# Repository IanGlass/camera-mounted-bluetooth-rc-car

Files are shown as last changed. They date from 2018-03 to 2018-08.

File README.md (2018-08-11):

# Camera Mounted Bluetooth Model Car

Embedded systems six-person project (known as "Wacky Racers") to design and implement a camera mounted, Bluetooth controlled, model car. The project had a requirement that three separate 4-layer boards (1:motor driver, 2:camera driver and 3:main/wifi communications) were developed each with their own microcontroller and communicated over a common I2C bus. STM32F4 microcontrollers were selected for the project.

## Camera Board

<p align="center">
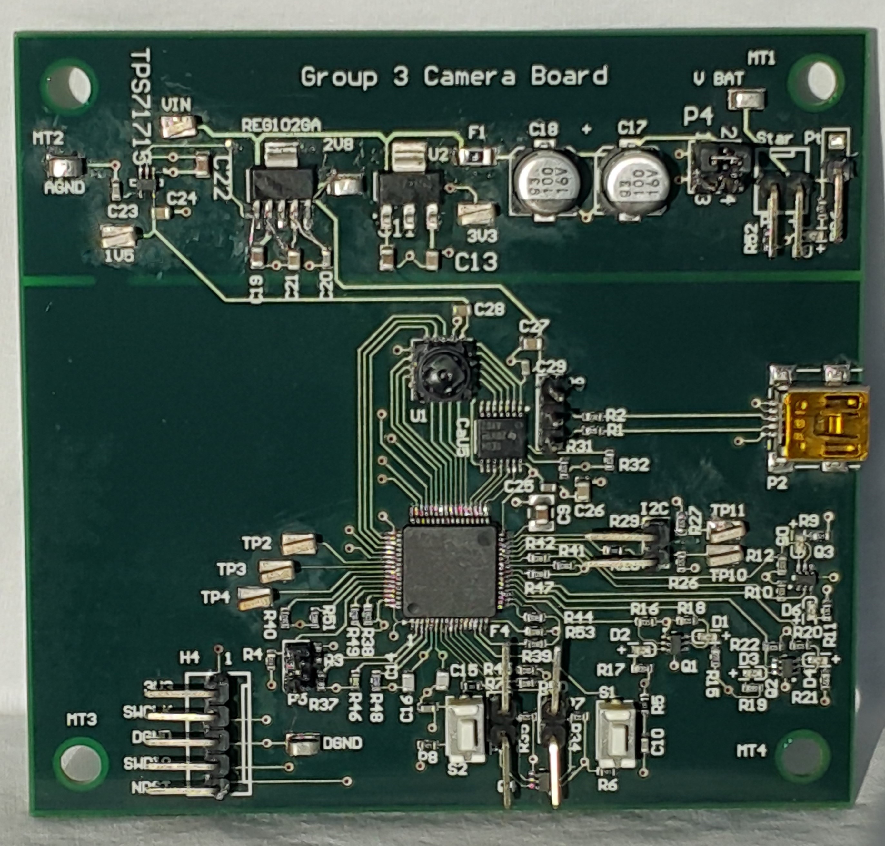
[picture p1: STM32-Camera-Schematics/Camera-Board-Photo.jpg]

</p>
<p align="center">
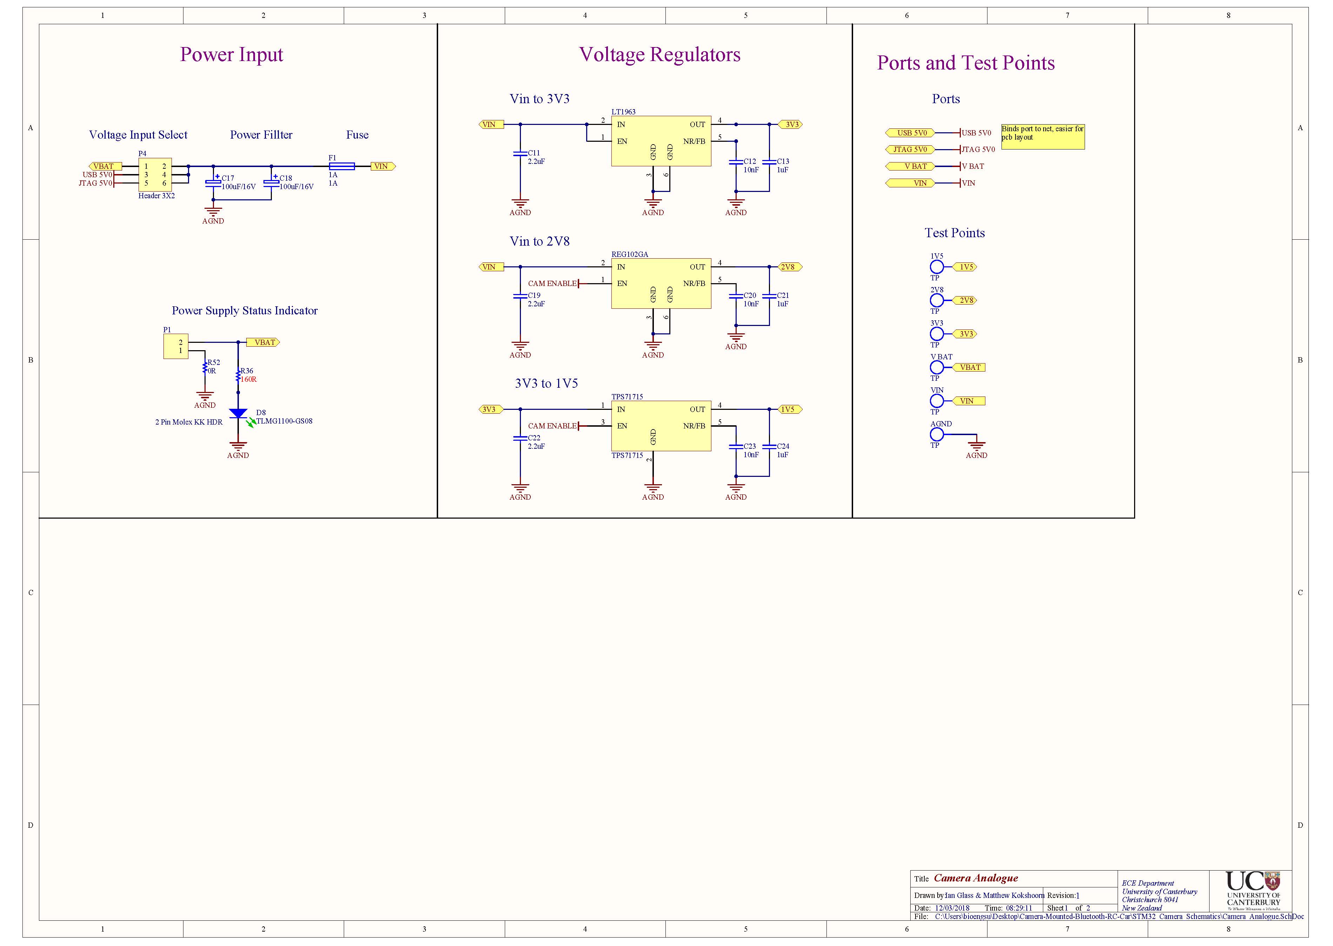
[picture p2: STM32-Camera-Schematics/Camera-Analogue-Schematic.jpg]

</p>
<p align="center">
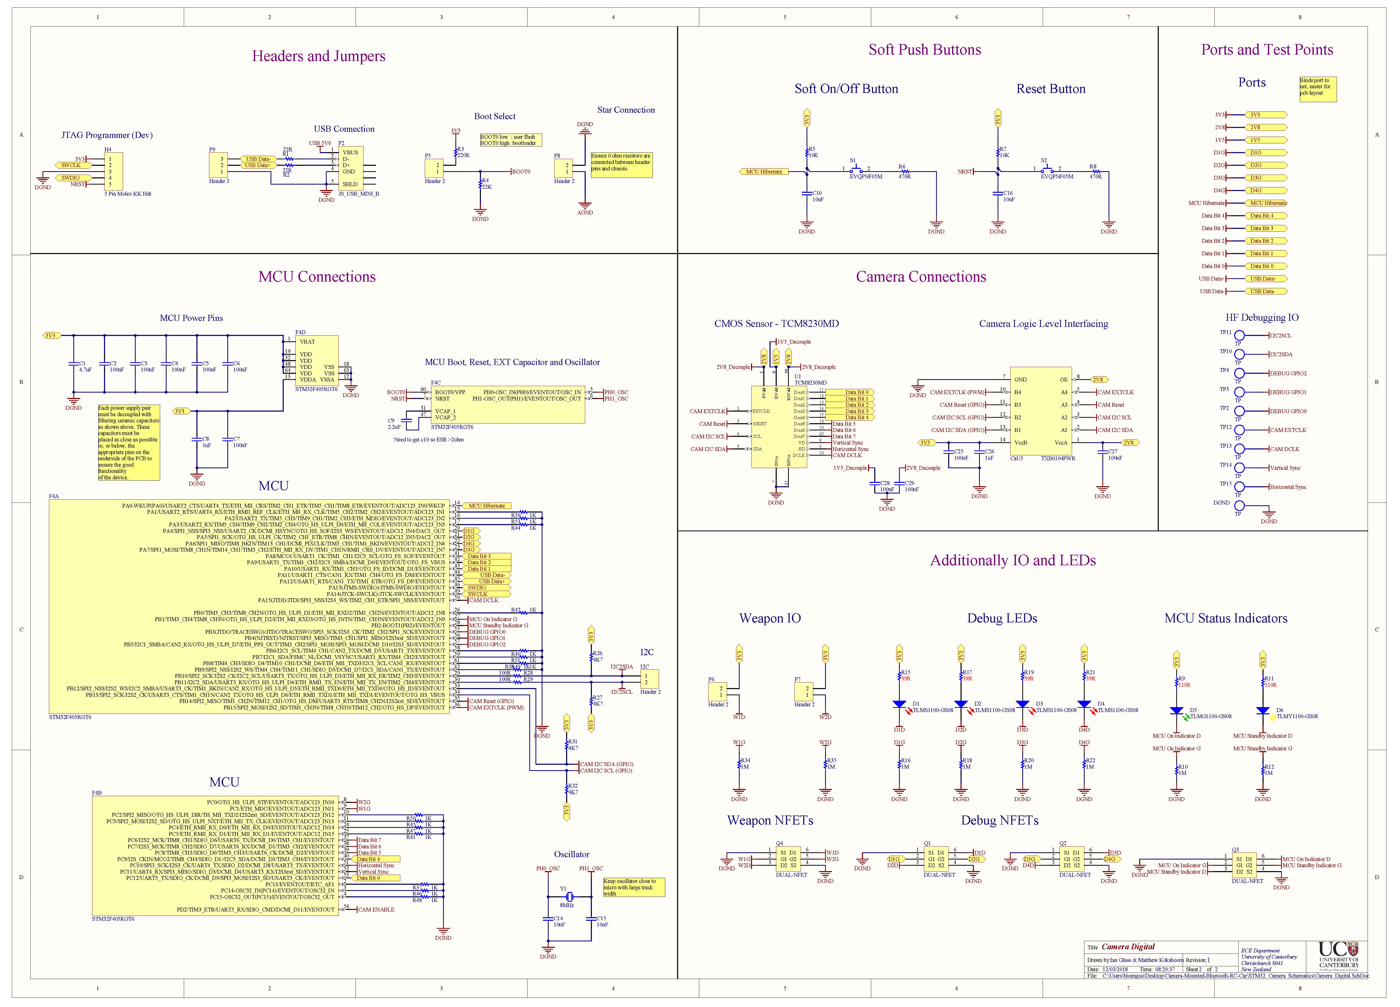
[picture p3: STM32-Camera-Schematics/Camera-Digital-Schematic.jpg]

</p>
<p align="center">
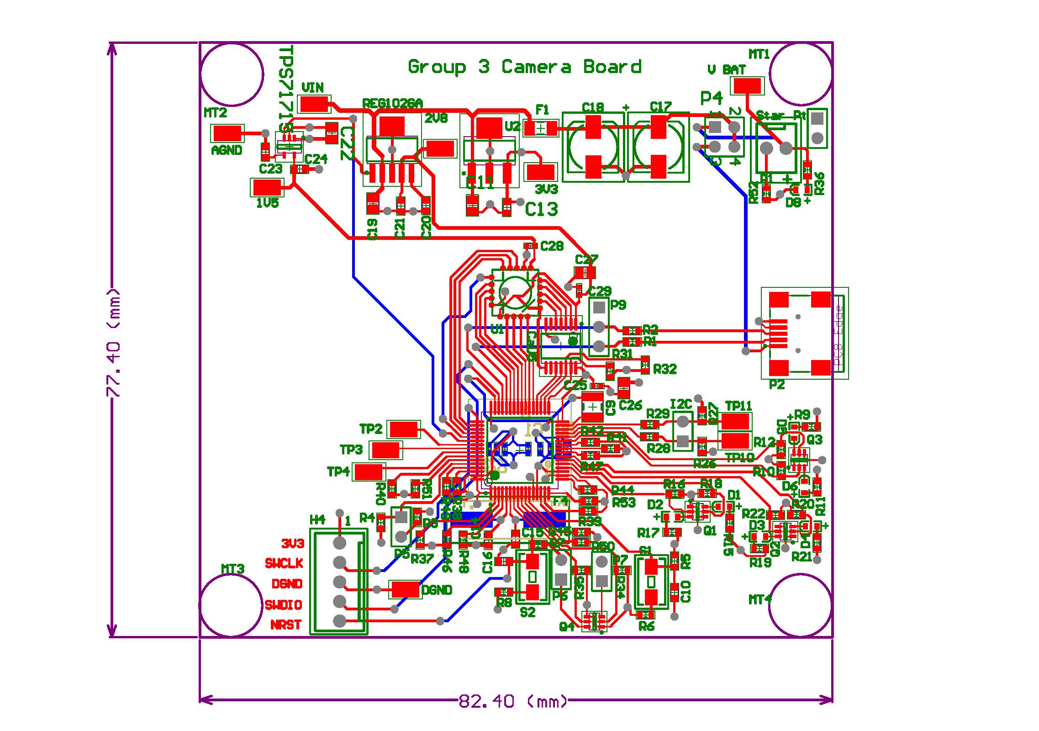
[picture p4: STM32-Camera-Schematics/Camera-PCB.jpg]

</p>

## Communications Board

<p align="center">
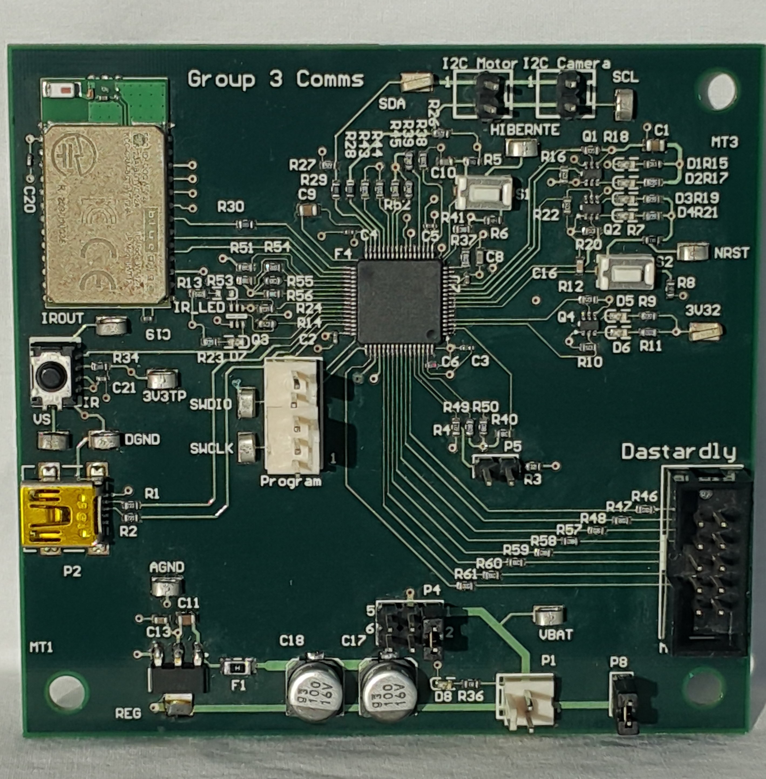
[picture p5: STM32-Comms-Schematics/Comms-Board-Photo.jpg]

</p>
<p align="center">
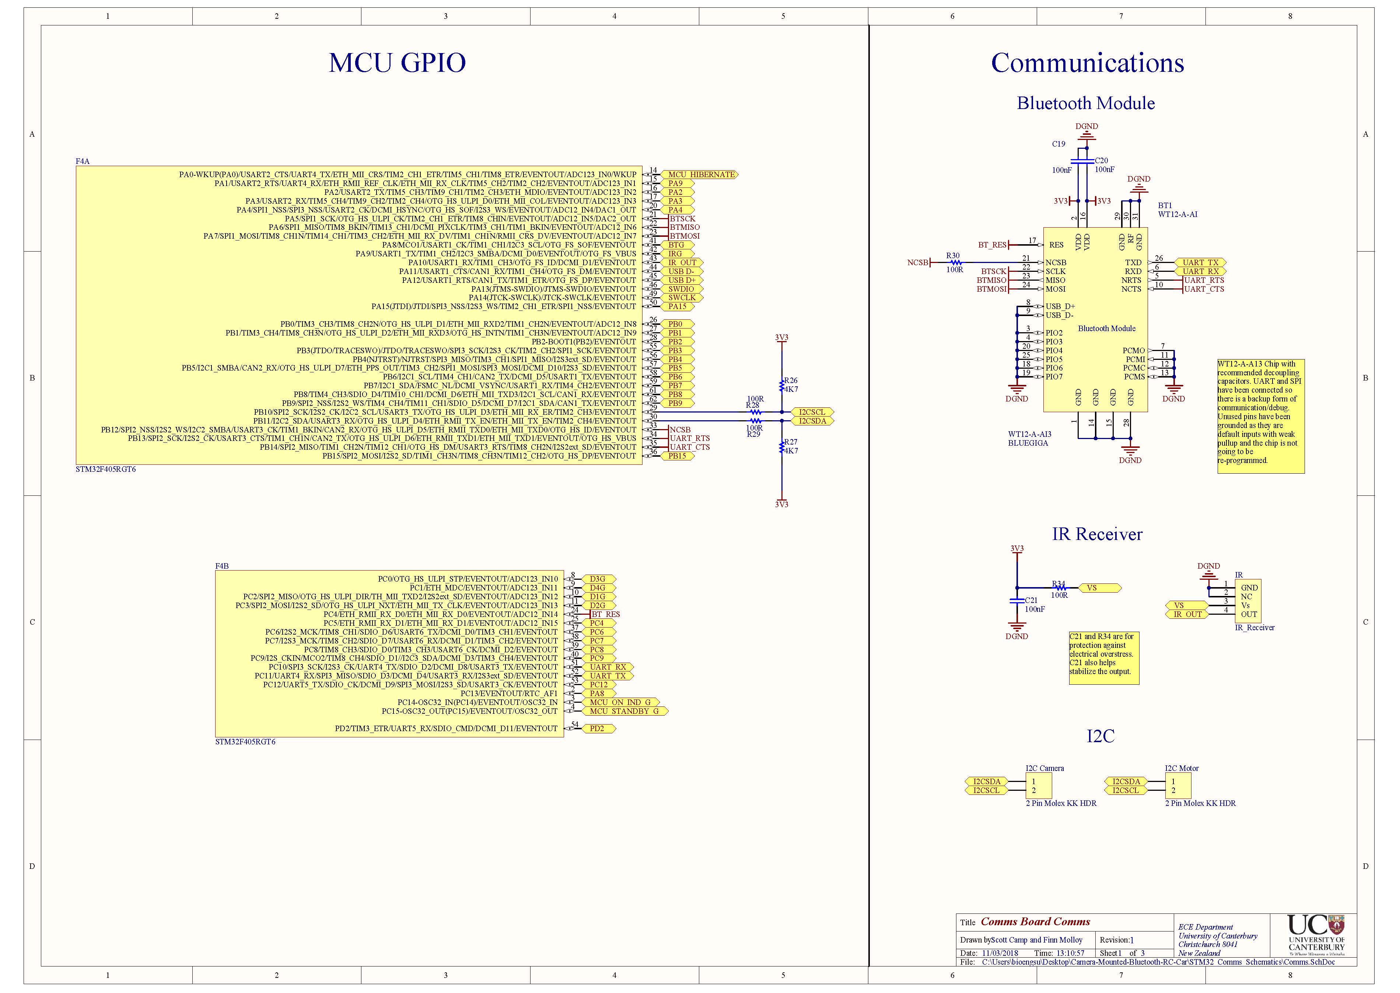
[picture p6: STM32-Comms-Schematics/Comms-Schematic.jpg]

</p>
<p align="center">
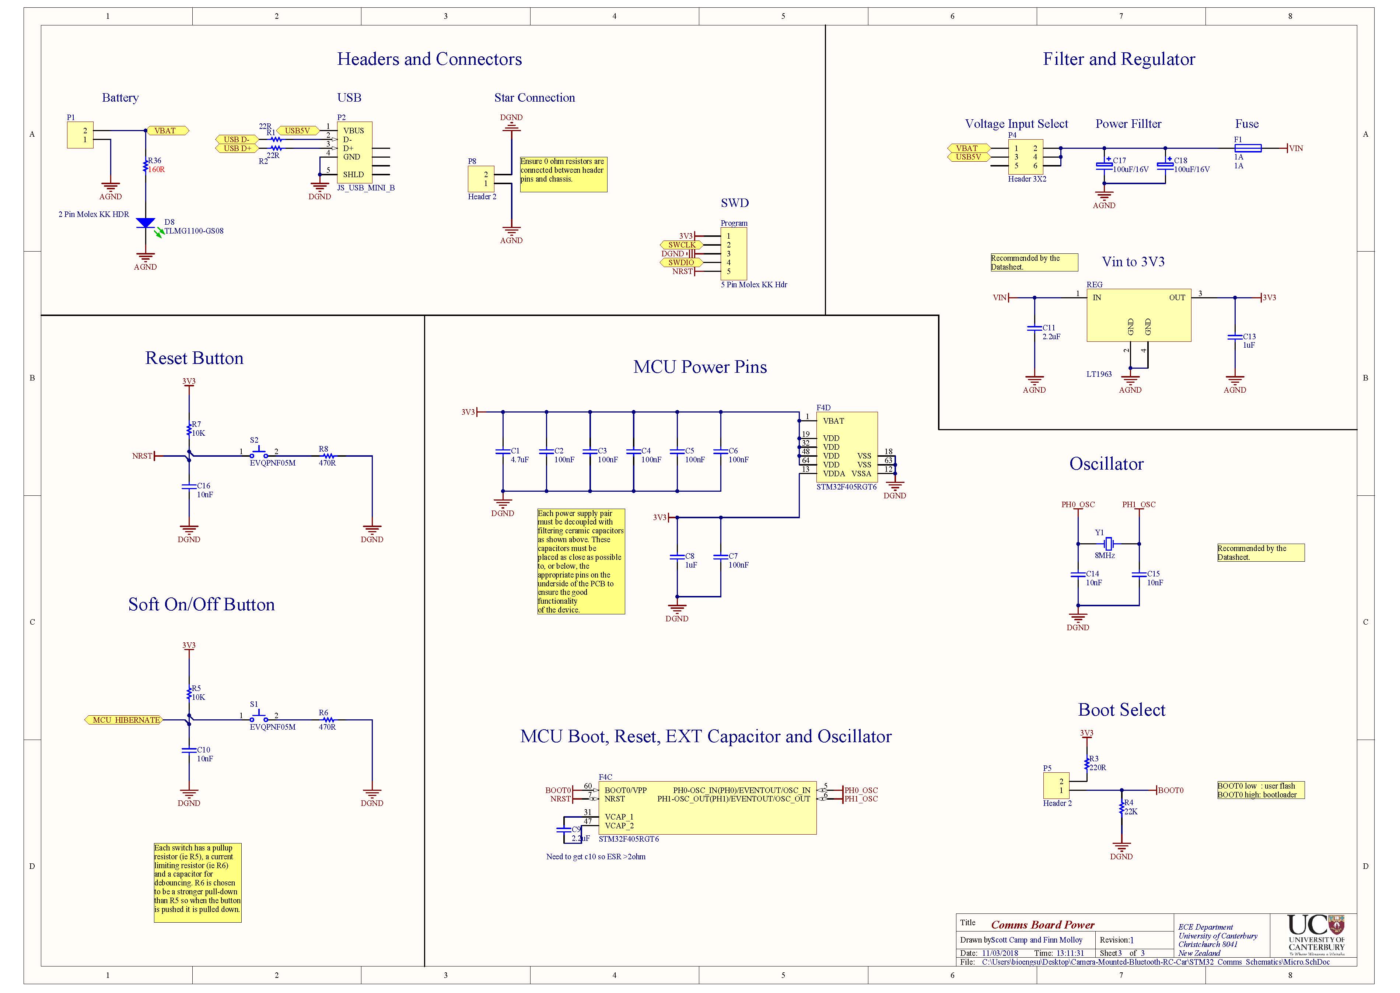
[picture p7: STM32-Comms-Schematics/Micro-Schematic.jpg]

</p>
<p align="center">
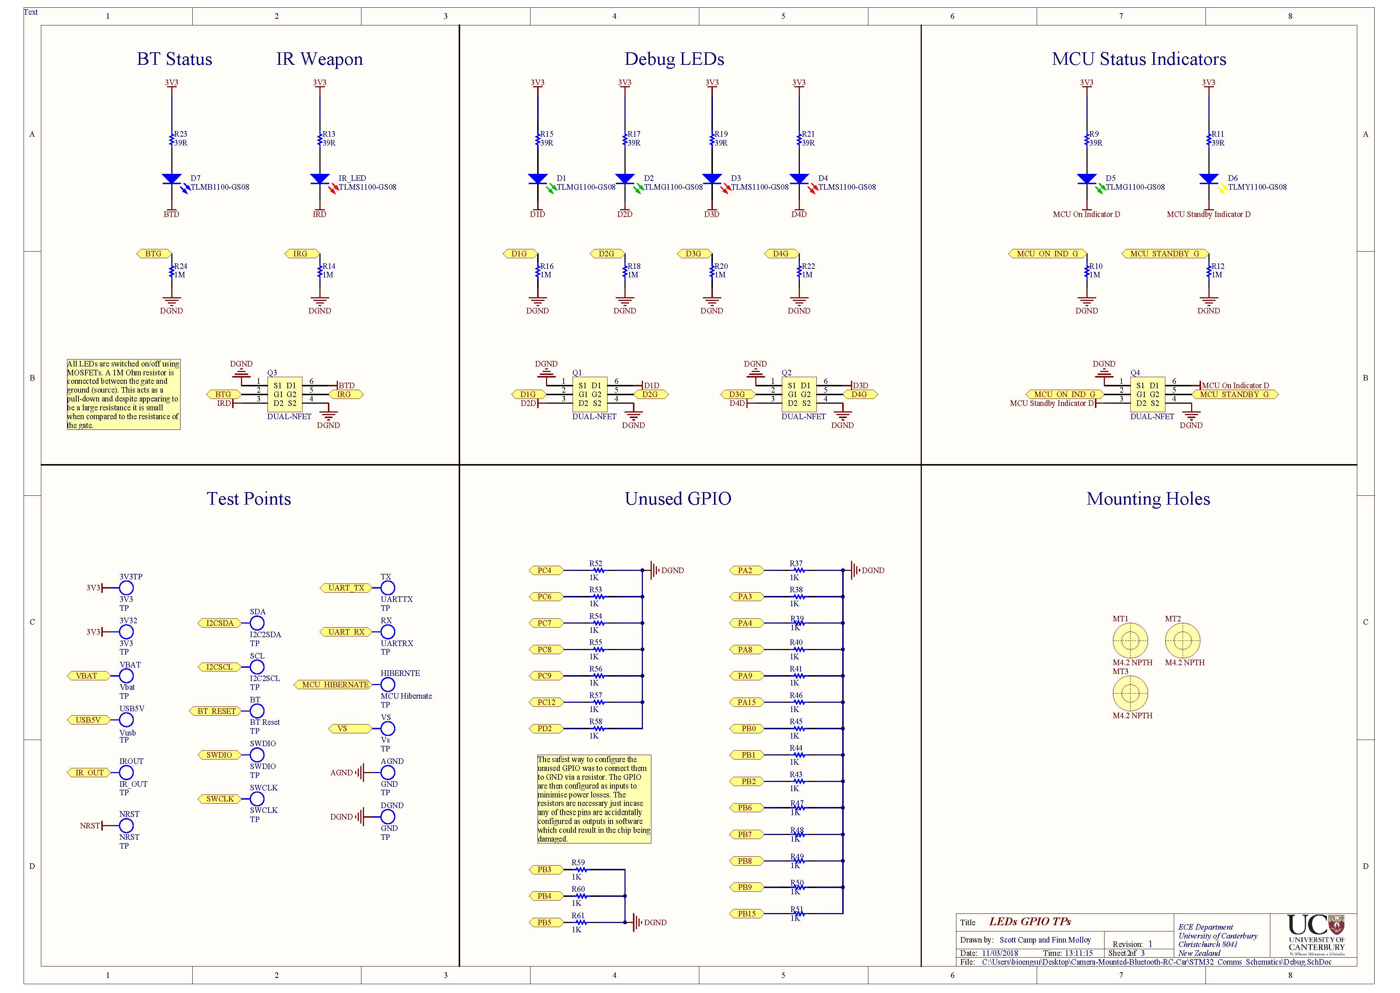
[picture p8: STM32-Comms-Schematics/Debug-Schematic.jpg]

</p>
<p align="center">
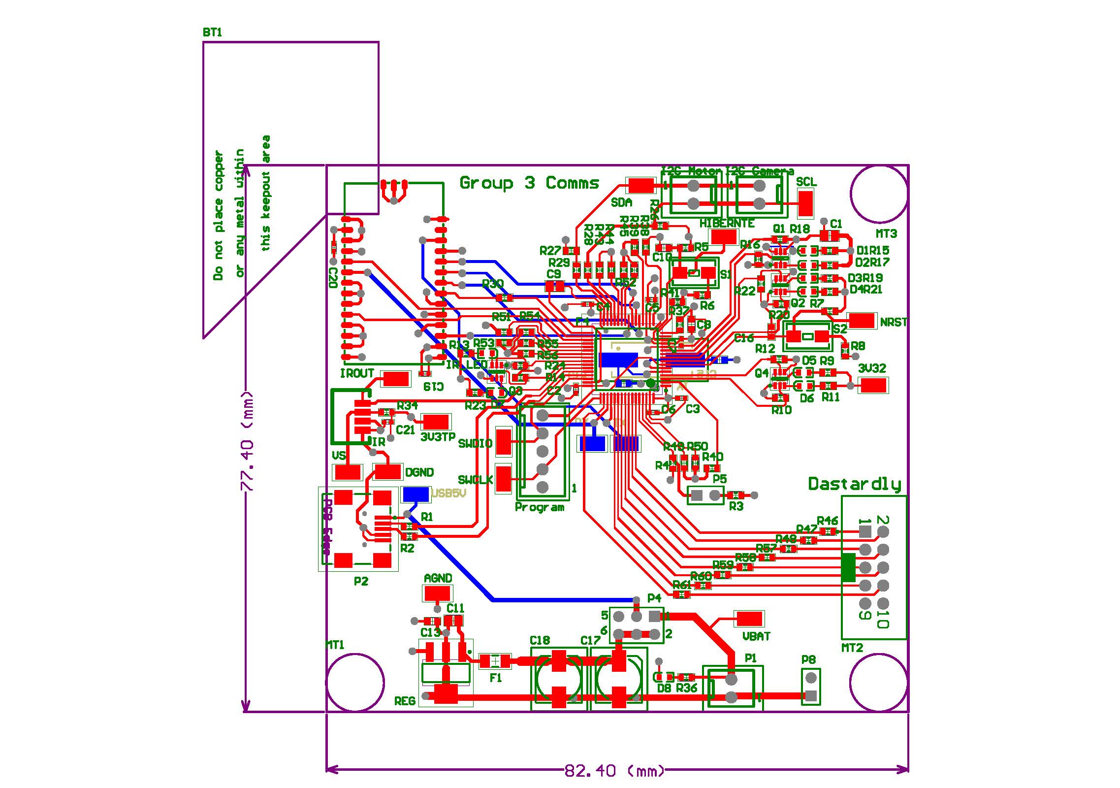
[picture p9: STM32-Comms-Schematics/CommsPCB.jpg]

</p>

## Motor Control / Power Board

<p align="center">
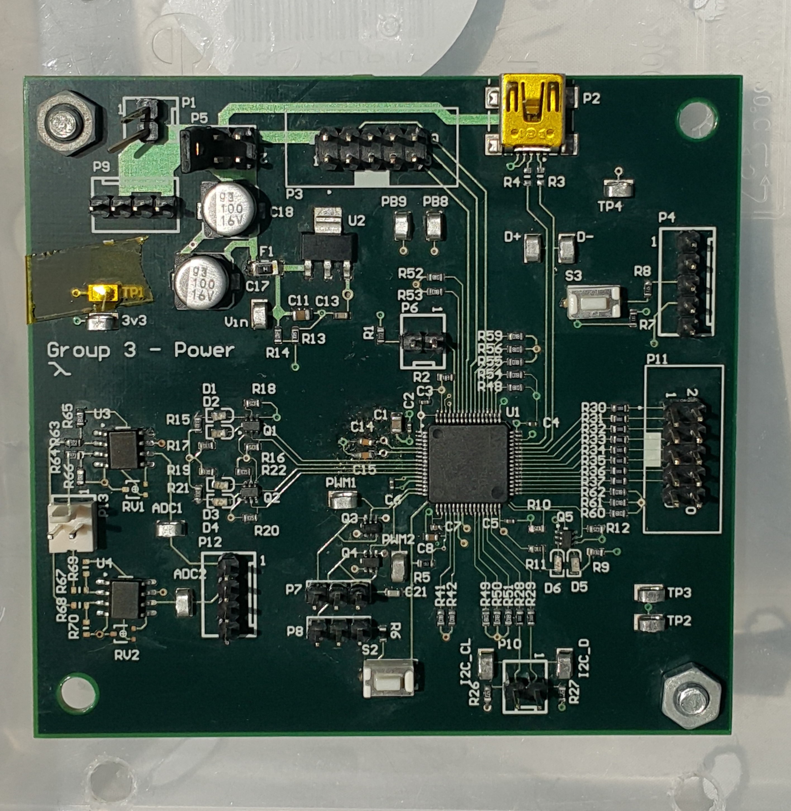
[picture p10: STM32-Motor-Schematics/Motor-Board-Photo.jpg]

</p>
<p align="center">
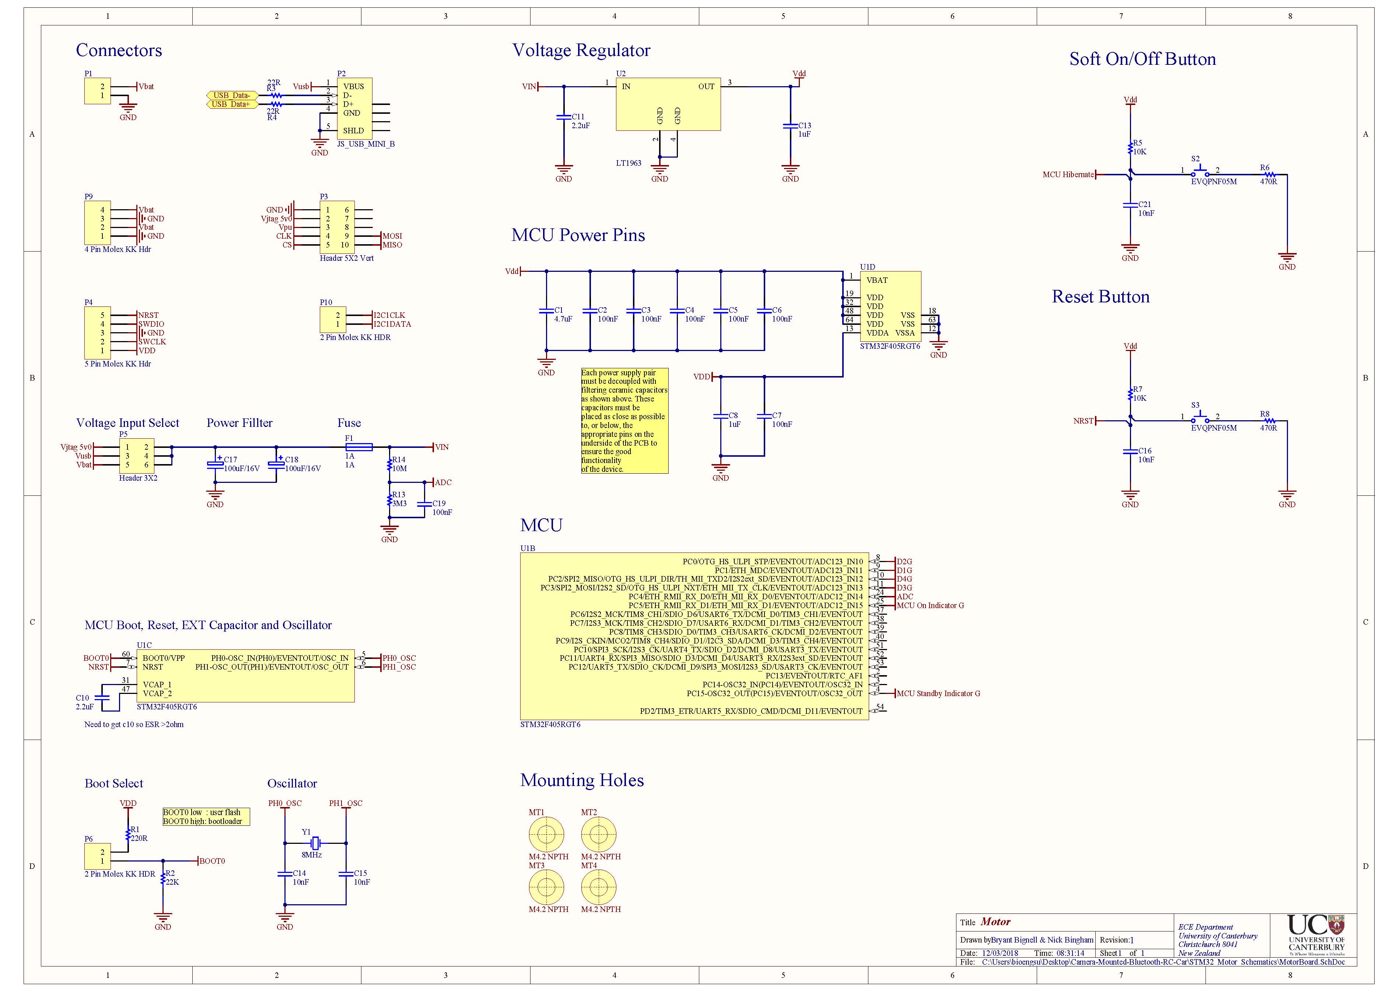
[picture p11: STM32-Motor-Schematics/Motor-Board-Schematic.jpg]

</p>
<p align="center">
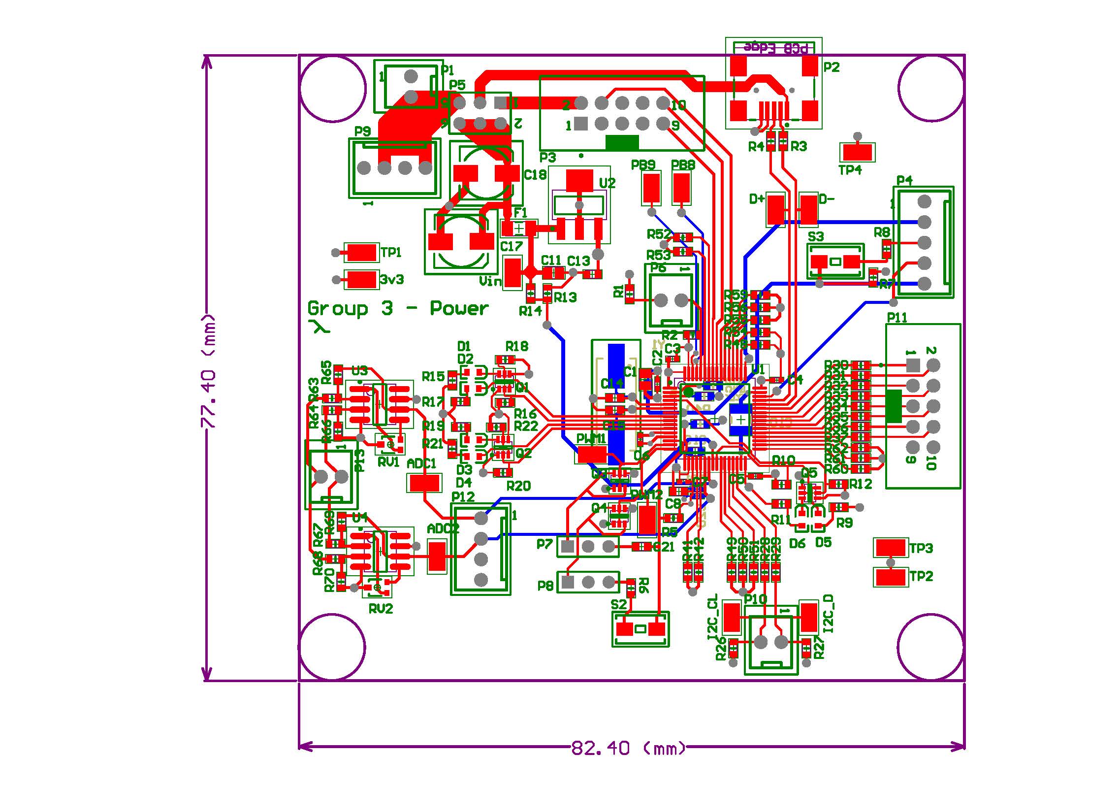
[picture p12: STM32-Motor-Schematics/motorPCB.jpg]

</p>

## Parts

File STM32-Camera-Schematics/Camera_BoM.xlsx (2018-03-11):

Bill of Materials |  |  | Camera Board
Source Data From: |  | CameraBoard.SchDoc
Project: |  | Wacky Racers
Variant: |  | None
Creation Date: | 4/4/2013 | 9:10:37 PM
Print Date: | 2018-03-11 | 16:38:15
Production Quantity: | 1
Currency | <none>
Footprint | Comment | Designator | Quantity
4.7uF | CAP CER 4.7uF Y5V -20% +80% 16V 0805 | C1 | 1
100nF | CAP CER 100nF X7R +-10% 16V 0402 | C2, C3, C4, C5, C6, C7, C25, C28, C29 | 9
1uF | CAP CER 1uF Y5V -20% +80% 16V 0603 | C8, C13, C21, C24 | 4
2.2uF | CAP CER 2.2uF Y5V -20% +80% 25V 0805 | C9 | 1
10nF | CAP CER 10nF X7R +-10% 50V 0603 | C10, C12, C14, C15, C16, C20, C23 | 7
2.2uF | CAP CER 2.2uF Y5V -20% +80% 25V 0805 | C11, C19, C22 | 3
100uF/16V | Nichcon WX series SMT Aluminium Electrolytic Cap | C17, C18 | 2
1uF | CAP CER 2.2uF Y5V -20% +80% 25V 0805 | C26 | 1
100nF | CAP CER 2.2uF Y5V -20% +80% 25V 0805 | C27 | 1
TXB0104PWR | VOLT-LEVEL TRANSLATOR 14TSSOP | CaU5 | 1
#NAME? | LED Red 0603, LED Red 0603, LED Red 0603, LED Red 0603, LED Green 0603, LED Yellow 0603, LED Green 0603 | D1, D2, D3, D4, D5, D6, D8 | 7
1A | Fuse 1.0A Very Fast Acting 1206 | F1 | 1
STM32F405RGT6 | ARM Cortex-M4 32b MCU+FPU, 210DMIP, 1024 kB Flash, 192+4 kB RAM, 51 I/Os, 64-pin LQFP, -40 to +85°C, Tray | F4 | 1
5 Pin Molex KK Hdr | CONN HEADER 5POS 2.54mm VERT_Thru Hole | H4 | 1
Header 2 | Header, 2-Pin | I2C, P5, P6, P7, P8 | 5
2 Pin Molex KK HDR | CONN HEADER 2POS 2.54mm VERT_Thru Hole | P1 | 1
JS_USB_MINI_B | USB 2.0, Right Angle, SMT, B Type, Receptacle, 5 Position, | P2 | 1
Header 3X2 | Header, 3-Pin, Dual row | P4 | 1
Header 3 | Header, 3-Pin | P9 | 1
DUAL-NFET |  | Q1, Q2, Q3, Q4 | 4
22R | RES 22 OHM 1/10W 5% 0603 SMD | R1, R2 | 2
220R | RES 220 OHM 1/10W 5% 0603 SMD | R3 | 1
22K | RES 22.0K OHM 1/10W 5% 0603 SMD | R4 | 1
10K | RES 10.0K OHM 1/10W 5% 0603 SMD | R5, R7 | 2
470R | RES 470 OHM 1/10W 5% 0603 SMD | R6, R8 | 2
110R | RES 110 OHM 1/10W 5% 0603 SMD | R9, R11 | 2
1M | RES 1.0M OHM 1/10W 5% 0603 SMD | R10, R12, R16, R18, R20, R22, R34, R35 | 8
39R | RES 110 OHM 1/10W 5% 0603 SMD | R15, R17, R19, R21 | 4
4K7 | RES 4.7K OHM 1/10W 5% 0603 SMD | R26, R27, R31, R32 | 4
100R | RES 100 OHM 1/10W 5% 0603 SMD | R28, R29 | 2
160R | RES 160 OHM 1/10W 5% 0603 SMD | R36 | 1
1K | RES 1.0K OHM 1/10W 5% 0603 SMD | R37, R38, R39, R40, R41, R42, R44, R45, R46, R47, R48, R49, R50, R51, R53 | 15
0R | RES 0.0 OHM 1/10W 5% 0603 SMD | R52 | 1
REG102GA | ULTRALOW-NOISE, HIGH PSRR, FAST, RF, 1A LOW-DROPOUT LINEAR REGULATORS | REG102GA | 1
EVQPNF05M | Panasonic 6 x 3.5mm SMD Light Touch Switch Type | S1, S2 | 2
LT1963 | ULTRALOW-NOISE, HIGH PSRR, FAST, RF, 1A LOW-DROPOUT LINEAR REGULATORS | TPS796xx | 1
TPS71715 | ULTRALOW-NOISE, HIGH PSRR, FAST, RF, 1A LOW-DROPOUT LINEAR REGULATORS | TPS71715 | 1
TCM8230MD | Toshiba I2C Camera | U1 | 1
8MHz | CRYSTAL 8.00 MHZ 18PF SMD | Y1 | 1
 |  |  | 105
Approved |  | Notes

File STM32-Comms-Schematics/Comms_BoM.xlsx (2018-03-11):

Bill of Materials |  |  | Comms Microcontroller and General
Source Data From: |  | WackyRacersComms.PrjPcb
Project: |  | WackyRacersComms.PrjPcb
Variant: |  | None
Creation Date: | 4/4/2013 | 8:41:36 PM
Print Date: | 2018-03-11 | 16:41:54
Production Quantity: | 1
Currency | <none>
Footprint | Comment | Designator | Quantity
#NAME? | BLUEGIGA - WT12-A-AI - BLUETOOTH MOD, V2.1, CLASS 2, 3MBPS | BT1 | 1
4.7uF | CAP CER 4.7uF Y5V -20% +80% 16V 0805 | C1 | 1
100nF | CAP CER 100nF X7R +-10% 16V 0402 | C2, C3, C4, C5, C6, C7, C19, C20, C21 | 9
1uF | CAP CER 1uF Y5V -20% +80% 16V 0603 | C8, C13 | 2
2.2uF | CAP CER 2.2uF Y5V -20% +80% 25V 0805 | C9, C11 | 2
10nF | CAP CER 10nF X7R +-10% 50V 0603 | C10, C14, C15, C16 | 4
100uF/16V | Nichcon WX series SMT Aluminium Electrolytic Cap | C17, C18 | 2
#NAME? | LED Green 0603, LED Green 0603, LED Red 0603, LED Red 0603, LED Green 0603, LED Yellow 0603, LED Blue 0603, LED Green 0603, LED Red 0603 | D1, D2, D3, D4, D5, D6, D7, D8, IR_LED | 9
1A | Fuse 1.0A Very Fast Acting 1206 | F1 | 1
STM32F405RGT6 | ARM Cortex-M4 32b MCU+FPU, 210DMIP, 1024 kB Flash, 192+4 kB RAM, 51 I/Os, 64-pin LQFP, -40 to +85°C, Tray | F4 | 1
2 Pin Molex KK HDR | CONN HEADER 2POS 2.54mm VERT_Thru Hole | I2C Camera, I2C Motor, P1 | 3
IR_Receiver | IR_Receiver | IR | 1
JS_USB_MINI_B | USB 2.0, Right Angle, SMT, B Type, Receptacle, 5 Position, | P2 | 1
Header 3X2 | Header, 3-Pin, Dual row | P4 | 1
Header 2 | Header, 2-Pin | P5, P8 | 2
5 Pin Molex KK Hdr | CONN HEADER 5POS 2.54mm VERT_Thru Hole | Program | 1
DUAL-NFET |  | Q1, Q2, Q3, Q4 | 4
22R | RES 22 OHM 1/10W 5% 0603 SMD | R1, R2 | 2
220R | RES 220 OHM 1/10W 5% 0603 SMD | R3 | 1
22K | RES 22.0K OHM 1/10W 5% 0603 SMD | R4 | 1
10K | RES 10.0K OHM 1/10W 5% 0603 SMD | R5, R7 | 2
470R | RES 470 OHM 1/10W 5% 0603 SMD | R6, R8 | 2
39R | RES 39 OHM 1/10W 5% 0603 SMD | R9, R11, R13, R15, R17, R19, R21, R23 | 8
1M | RES 1.0M OHM 1/10W 5% 0603 SMD | R10, R12, R14, R16, R18, R20, R22, R24 | 8
4K7 | RES 4.7K OHM 1/10W 5% 0603 SMD | R26, R27 | 2
100R | RES 100 OHM 1/10W 5% 0603 SMD | R28, R29, R30, R34 | 4
160R | RES 160 OHM 1/10W 5% 0603 SMD | R36 | 1
1K | RES 1.0K OHM 1/10W 5% 0603 SMD | R37, R38, R39, R40, R41, R43, R44, R45, R46, R47, R48, R49, R50, R51, R52, R53, R54, R55, R56, R57, R58, R59, R60, R61 | 24
LT1963 |  | REG | 1
EVQPNF05M | Panasonic 6 x 3.5mm SMD Light Touch Switch Type | S1, S2 | 2
8MHz | CRYSTAL 8.00 MHZ 18PF SMD | Y1 | 1
 |  |  | 104
Approved |  | Notes

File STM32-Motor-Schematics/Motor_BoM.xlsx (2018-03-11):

Bill of Materials |  |  | Wacky Races Motor Module
Source Data From: |  | PowerBoard_bryant_2013_04_04.SchDoc
Project: |  | Free Documents
Variant: |  | None
Creation Date: | 4/4/2013 | 7:29:26 PM
Print Date: | 2018-03-11 | 16:44:01
Production Quantity: | 1
Currency | <none>
Footprint | Comment | Designator | Quantity
4.7uF | CAP CER 4.7uF Y5V -20% +80% 16V 0805 | C1 | 1
100nF | CAP CER 100nF X7R +-10% 16V 0402 | C2, C3, C4, C5, C6, C7 | 6
1uF | CAP CER 1uF Y5V -20% +80% 16V 0603 | C8, C13 | 2
2.2uF | CAP CER 2.2uF Y5V -20% +80% 25V 0805 | C10 | 1
2.2uF | CAP CER 2.2uF Y5V -20% +80% 25V 0805 | C11 | 1
10nF | CAP CER 10nF X7R +-10% 50V 0603 | C14, C15, C16, C21 | 4
100uF/16V | Nichcon WX series SMT Aluminium Electrolytic Cap | C17, C18 | 2
100nF | CAP CER 100nF X7R +-10% 50V 0603 | C19 | 1
1A | Fuse 1.0A Very Fast Acting 1206 | F1 | 1
Value | CONN HEADER 2POS 2.54mm VERT_Thru Hole | P1 | 1
JS_USB_MINI_B | USB 2.0, Right Angle, SMT, B Type, Receptacle, 5 Position, | P2 | 1
Header 5X2 Vert | IDC Header, 2,54mm, 10-Pin, Vert | P3 | 1
5 Pin Molex KK Hdr | CONN HEADER 5POS 2.54mm VERT_Thru Hole | P4 | 1
Header 3X2 | Header, 3-Pin, Dual row | P5 | 1
2 Pin Molex KK HDR | CONN HEADER 2POS 2.54mm VERT_Thru Hole | P6, P10 | 2
4 Pin Molex KK Hdr | CONN HEADER 4POS 2.54mm VERT_Thru Hole | P9 | 1
220R | RES 220 OHM 1/10W 5% 0603 SMD | R1 | 1
22K | RES 22.0K OHM 1/10W 5% 0603 SMD | R2 | 1
22R | RES 22 OHM 1/10W 5% 0603 SMD | R3, R4 | 2
10K | RES 10.0K OHM 1/10W 5% 0603 SMD | R5, R7 | 2
470R | RES 470 OHM 1/10W 5% 0603 SMD | R6, R8 | 2
3M3 | RES 3.3M OHM 1/10W 5% 0603 SMD | R13 | 1
10M | RES 10.0M OHM 1/10W 5% 0603 SMD | R14 | 1
EVQPNF05M | Panasonic 6 x 3.5mm SMD Light Touch Switch Type | S2, S3 | 2
STM32F405RGT6 | ARM Cortex-M4 32b MCU+FPU, 210DMIP, 1024 kB Flash, 192+4 kB RAM, 51 I/Os, 64-pin LQFP, -40 to +85°C, Tray | U1 | 1
LT1963 |  | U2 | 1
8MHz | CRYSTAL 8.00 MHZ 18PF SMD | Y1 | 1
 |  |  | 42
Approved |  | Notes

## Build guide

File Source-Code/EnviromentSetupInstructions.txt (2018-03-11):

1) Download Attolic Embedded Workbench (This is used for programming/debugging via the SWD link)
	http://www.atollic.com/index.php/download/truestudio-for-arm 

	- Open Appropriate Workspace I have set up.

		- Comms
		- Camera
		- Motor 
		- Dev Board

Programming Hardware setup:

	- Grab a Dev board and some female to female cords (got heaps)
	- Find the SWD header 6 pin header (Calling the end with the dot 1):

		from Dev board to Wacky Racers boards:
		- Pin 1/??? 	to ??? (Dev Board:GND)    ------- N/A
		- Pin 2/T_JTCK 	to SWCLK (Dev Board:PA14)
		- Pin 3/GND	to DGND (Dev Board:GND)
		- Pin 4/T_JTMS  to SWDIO (Dev Board:PA13)
		- Pin 5/T_NRST 	to NRST (Dev Board:NRST)
		- Pin 6/T_SWO 	to GND (Dev Board:PB3)    ------- N/A

2) Download and Install Tera Term (This is used for uart communication with the chip)
	- Go New Connection -> Serial Connection -> USB Serial Port (COMX)
	- Setup -> Serial Port Baud Rate -> 115200 .
	- Setup -> Terminal -> Make syre recieve and transmit are 'CR' under new-line and encavble local echo.

	To Enable Serial Comms with MCU enter the following in the terminal (By \n I mean enter) 'm\n','3\n','9\n','1\n','1\n','2\n' then '(2)'

	Ensure the following hardware Hardware- Connection (DEV BOARD) to Bus Pirate 
		- MISO (bus Pirate) to PA2 (Usart2 Tx) (SCL)
		- MOSI (bus pirate) to PA3 (Usart2 Rx)
		- GND to GND

3)	Some Notes about Common Code:

	- I have developed some code for printing to the terminal via the dev board and will
	  port this out 64 pin controller when we begin programming. (Thurday Week 4).

	- I am working on I2C code between two dev boards and then I will port to new MCU too. (Thursday Week 4).

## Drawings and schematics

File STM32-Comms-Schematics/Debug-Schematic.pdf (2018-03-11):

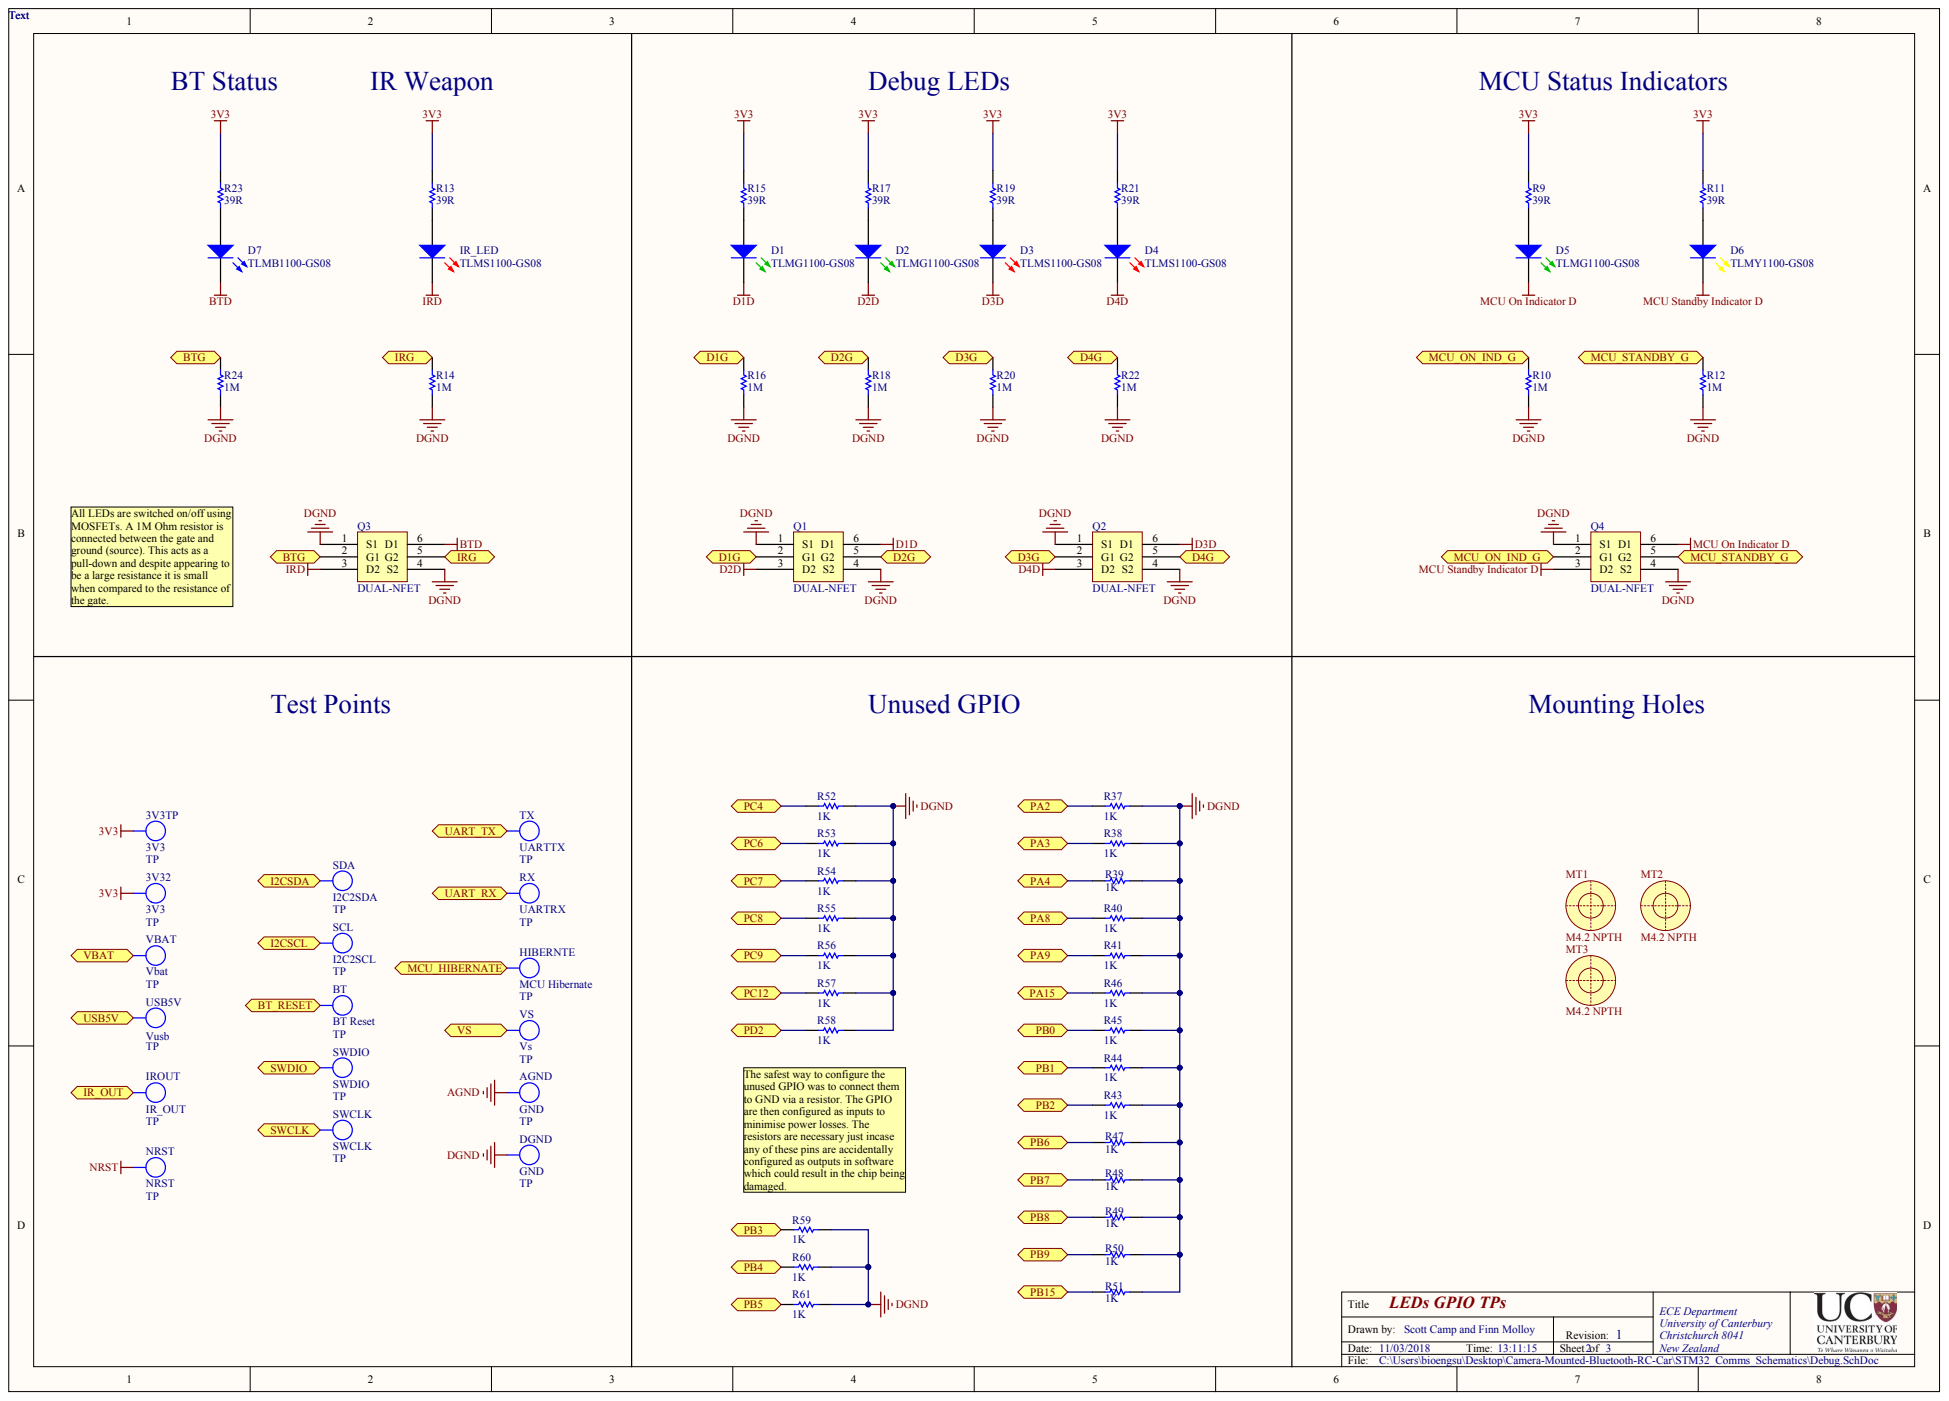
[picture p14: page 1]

All LEDs are switched on/off using
MOSFETs. A 1M Ohm resistor is
connected between the gate and
ground (source). This acts as a
pull-down and despite appearing to
be a large resistance it is small
when compared to the resistance of
the gate.

The safest way to configure the
unused GPIO was to connect them
to GND via a resistor. The GPIO
are then configured as inputs to
minimise power losses. The
resistors are necessary just incase
any of these pins are accidentally
configured as outputs in software
which could result in the chip being
damaged.

LEDs GPIO TPs Title | ECE Department University of Canterbury Christchurch 8041 New Zealand

Drawn by: Scott Camp and Finn Molloy 13:11:15 | Revision: 1 11/03/2018

Date: Time: | Sheet of 2 3

C:\Users\bioengsu\Desktop\Camera-Mounted-Bluetooth-RC-Car\STM32_Comms_Schematics\Debug.SchDoc

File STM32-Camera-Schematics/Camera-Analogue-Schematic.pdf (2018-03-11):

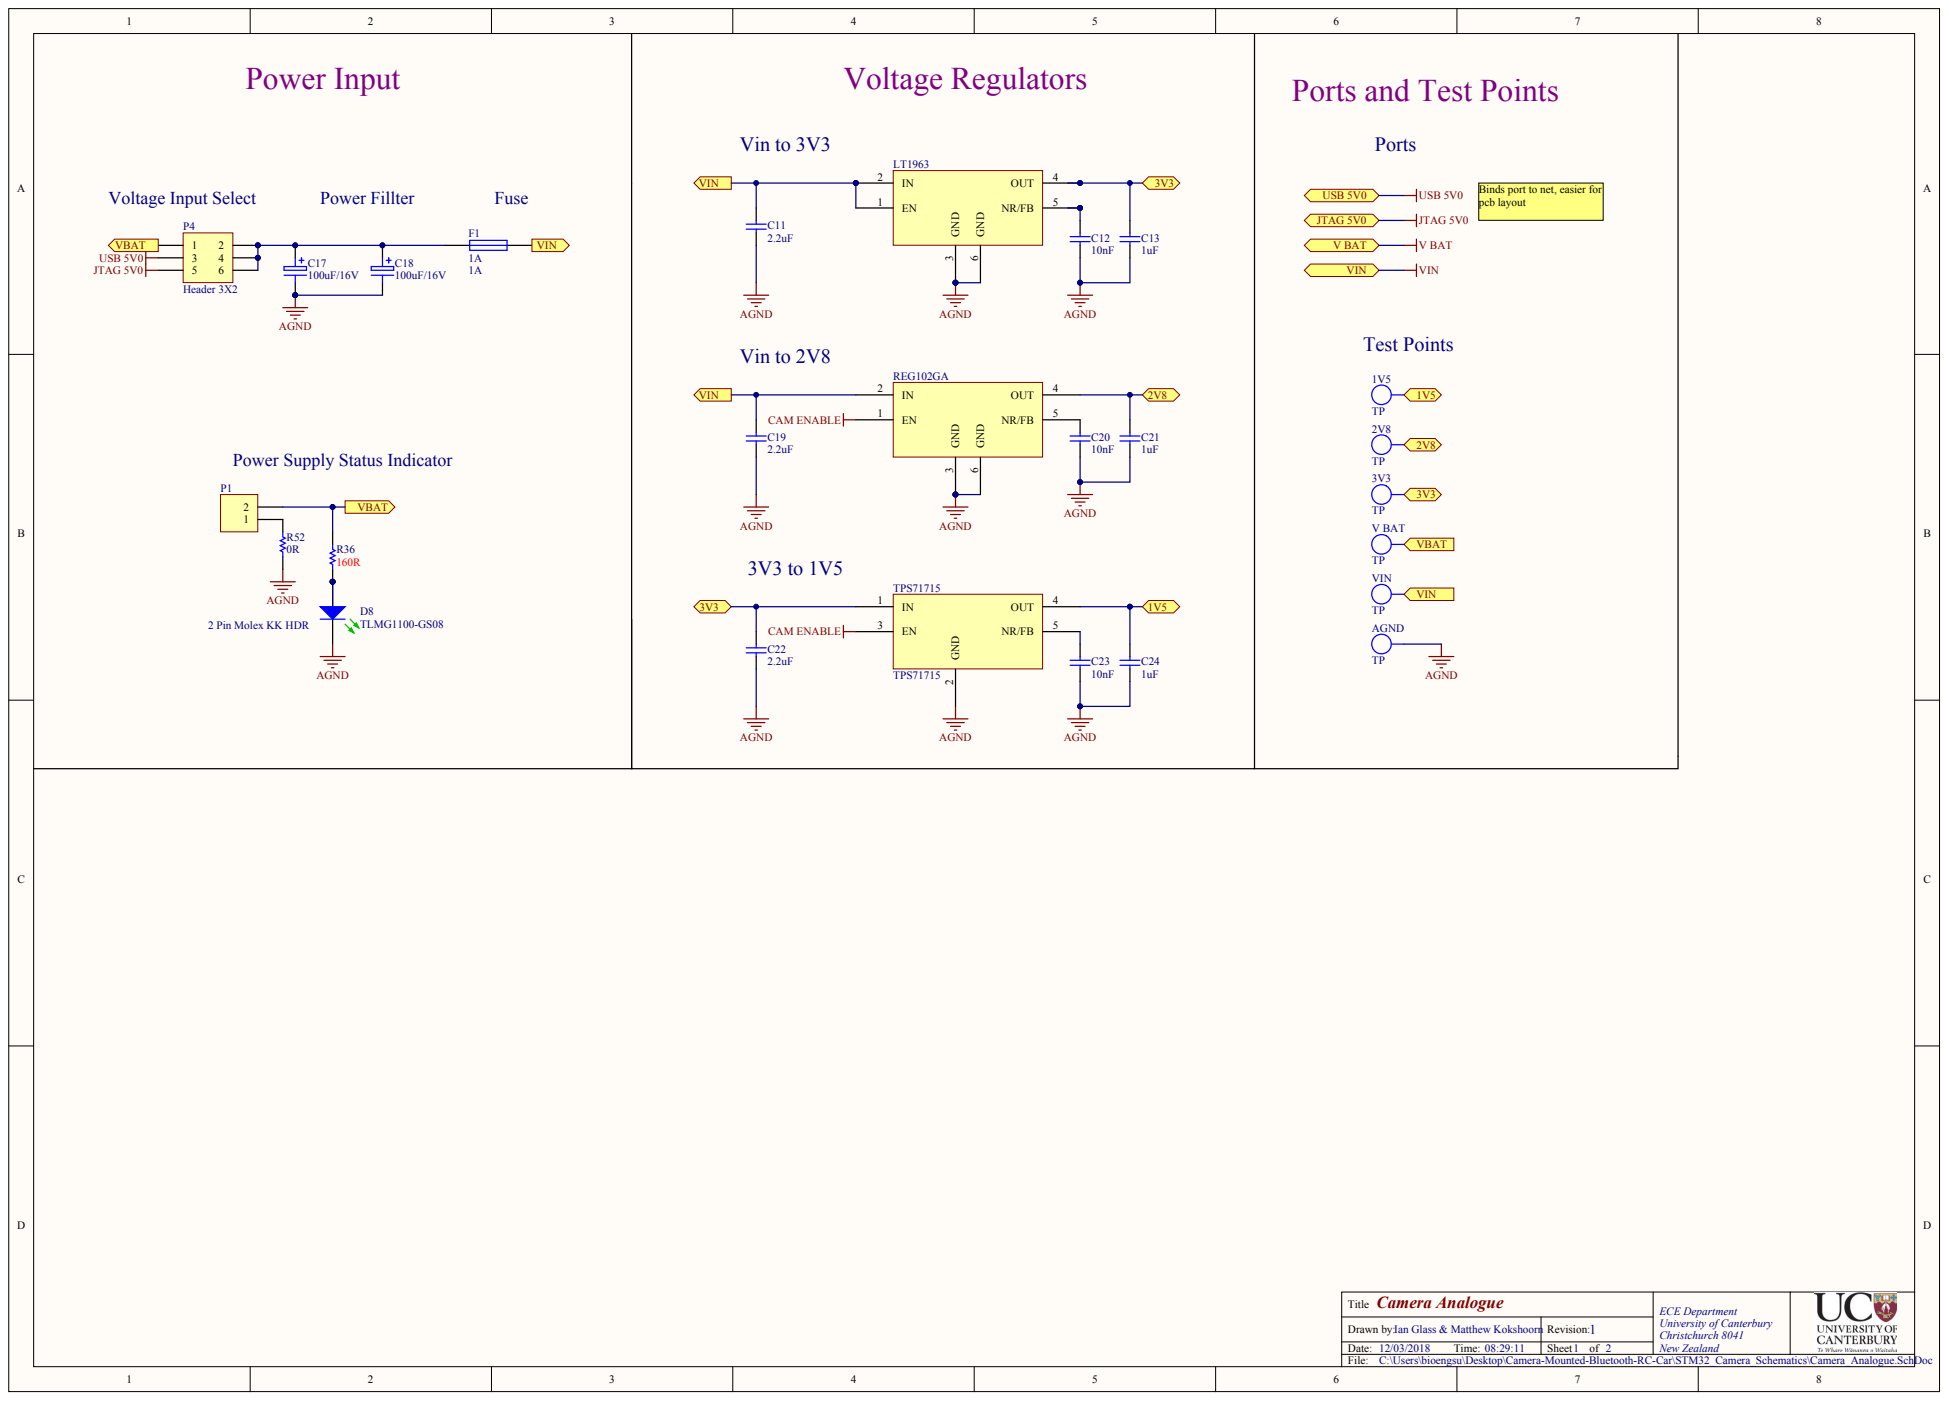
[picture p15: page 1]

Ports and Test Points Voltage Regulators

Binds port to net, easier for
pcb layout

Power Supply Status Indicator

2 Pin Molex KK HDR 12

Camera Analogue Title | ECE Department University of Canterbury Christchurch 8041 New Zealand

Drawn by: Ian Glass & Matthew Kokshoorn | Revision: 1

Date: 12/03/2018 Time: 08:29:11 | Sheet 1 of 2

C:\Users\bioengsu\Desktop\Camera-Mounted-Bluetooth-RC-Car\STM32_Camera_Schematics\Camera_Analogue.SchDoc

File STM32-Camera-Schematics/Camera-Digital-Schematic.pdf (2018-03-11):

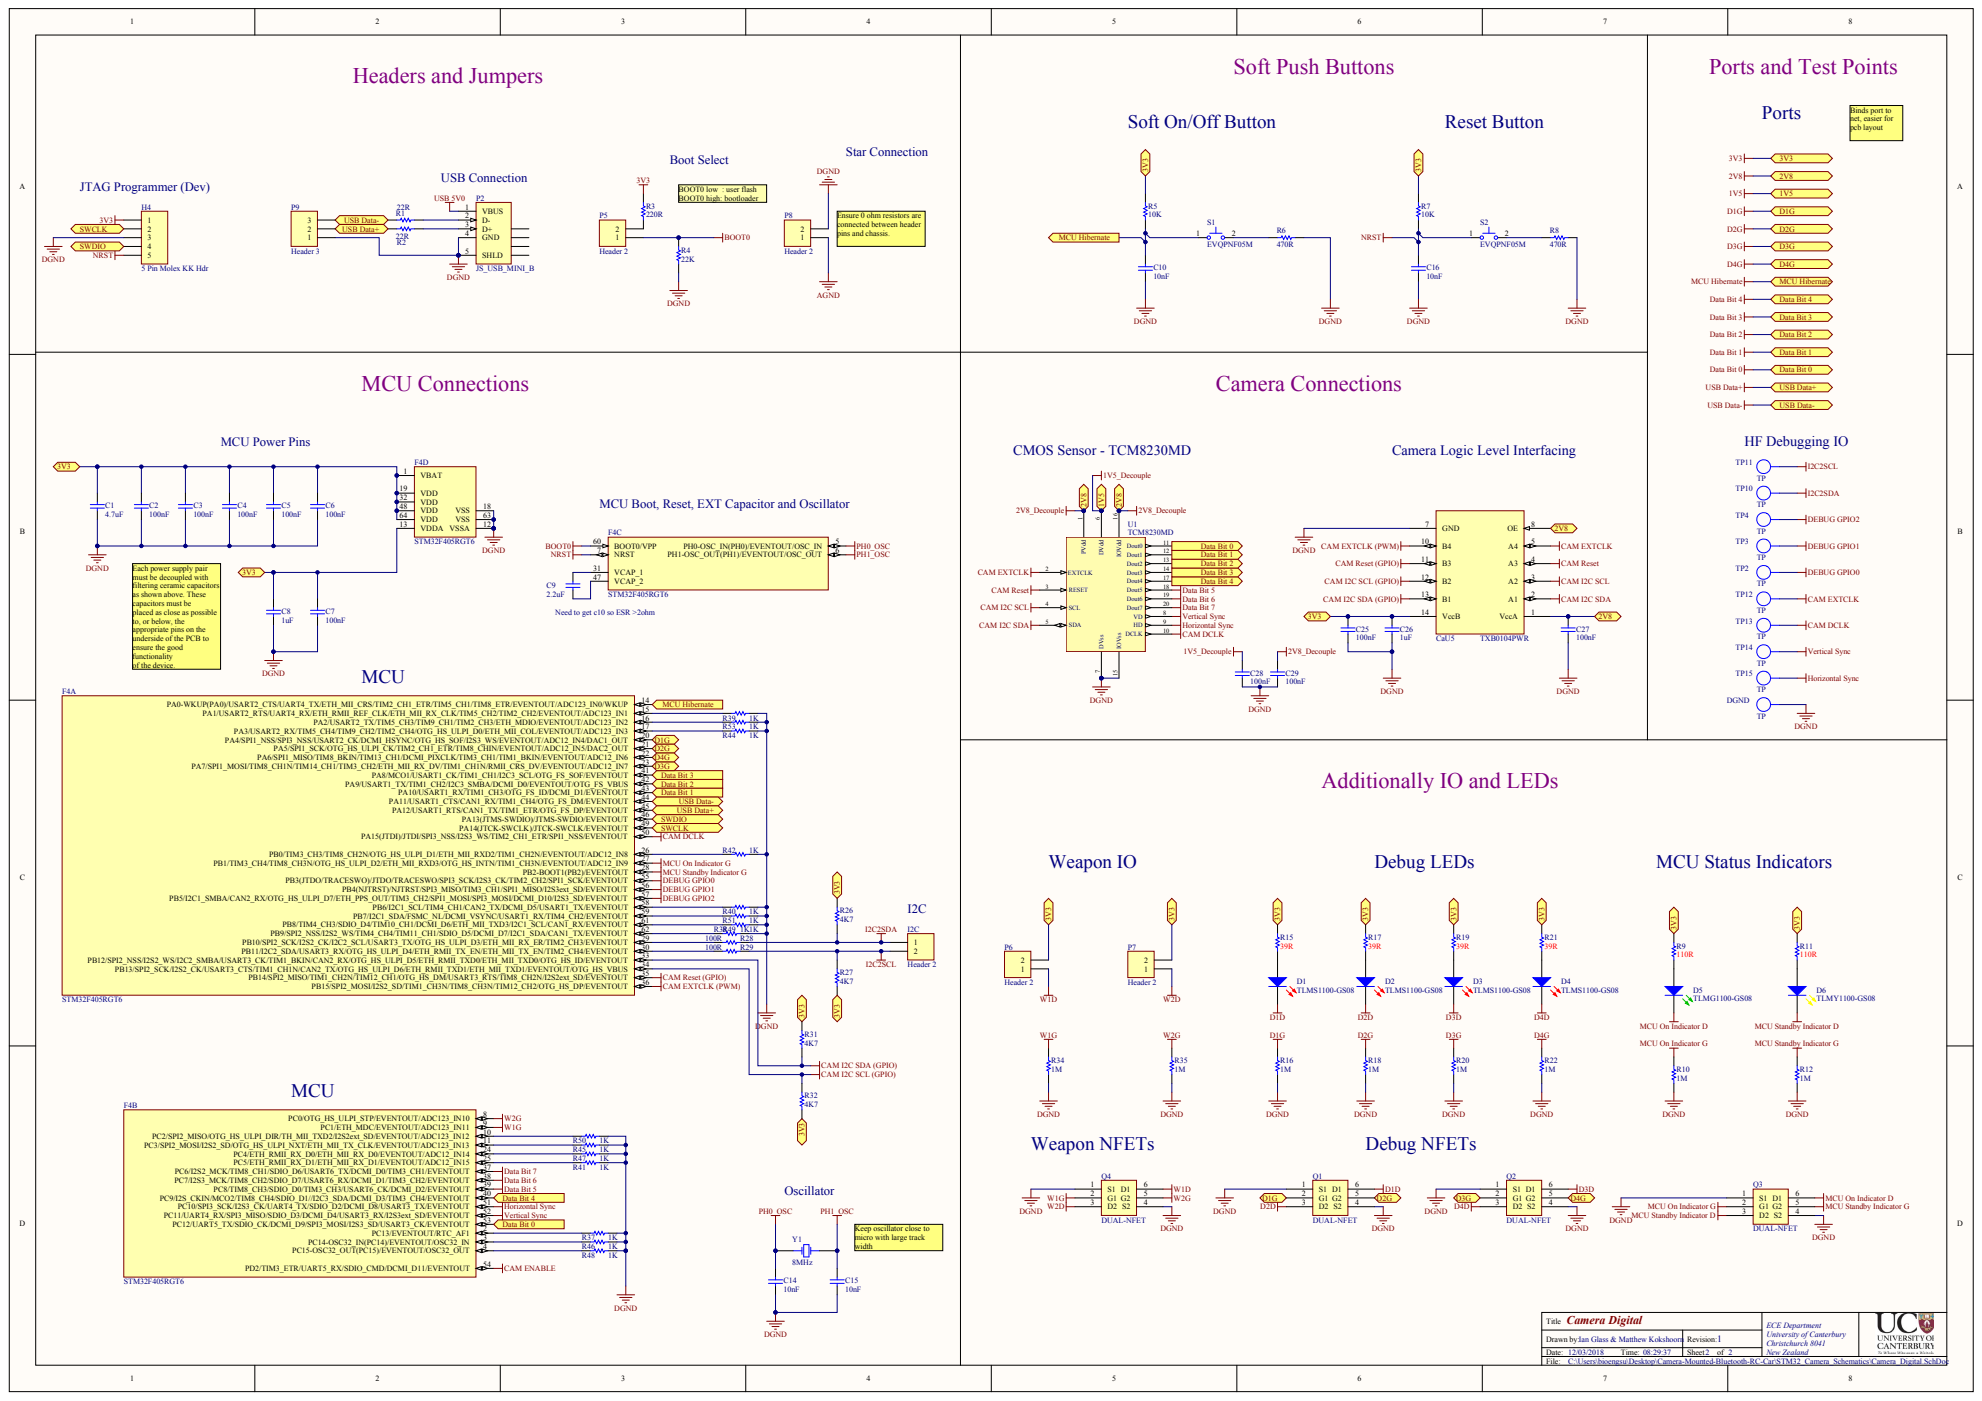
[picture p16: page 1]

Soft On/Off Button

Ensure 0 ohm resistors are
connected between header
pins and chassis.

Camera Logic Level Interfacing

MCU Boot, Reset, EXT Capacitor and Oscillator

must be decoupled with
filtering ceramic capacitors
as shown above. These
capacitors must be
placed as close as possible
to, or below, the

Need to get c10 so ESR >2ohm

appropriate pins on the
underside of the PCB to
ensure the good
functionality
of the device.

Additionally IO and LEDs

Keep oscillator close to
micro with large track
width

Drawn by:
Date:
C:\Users\bioengsu\Desktop\Camera-Mounted-Bluetooth-RC-Car\STM32_Camera_Schematics\Camera_Digital.SchDoc

Ian Glass & Matthew Kokshoorn

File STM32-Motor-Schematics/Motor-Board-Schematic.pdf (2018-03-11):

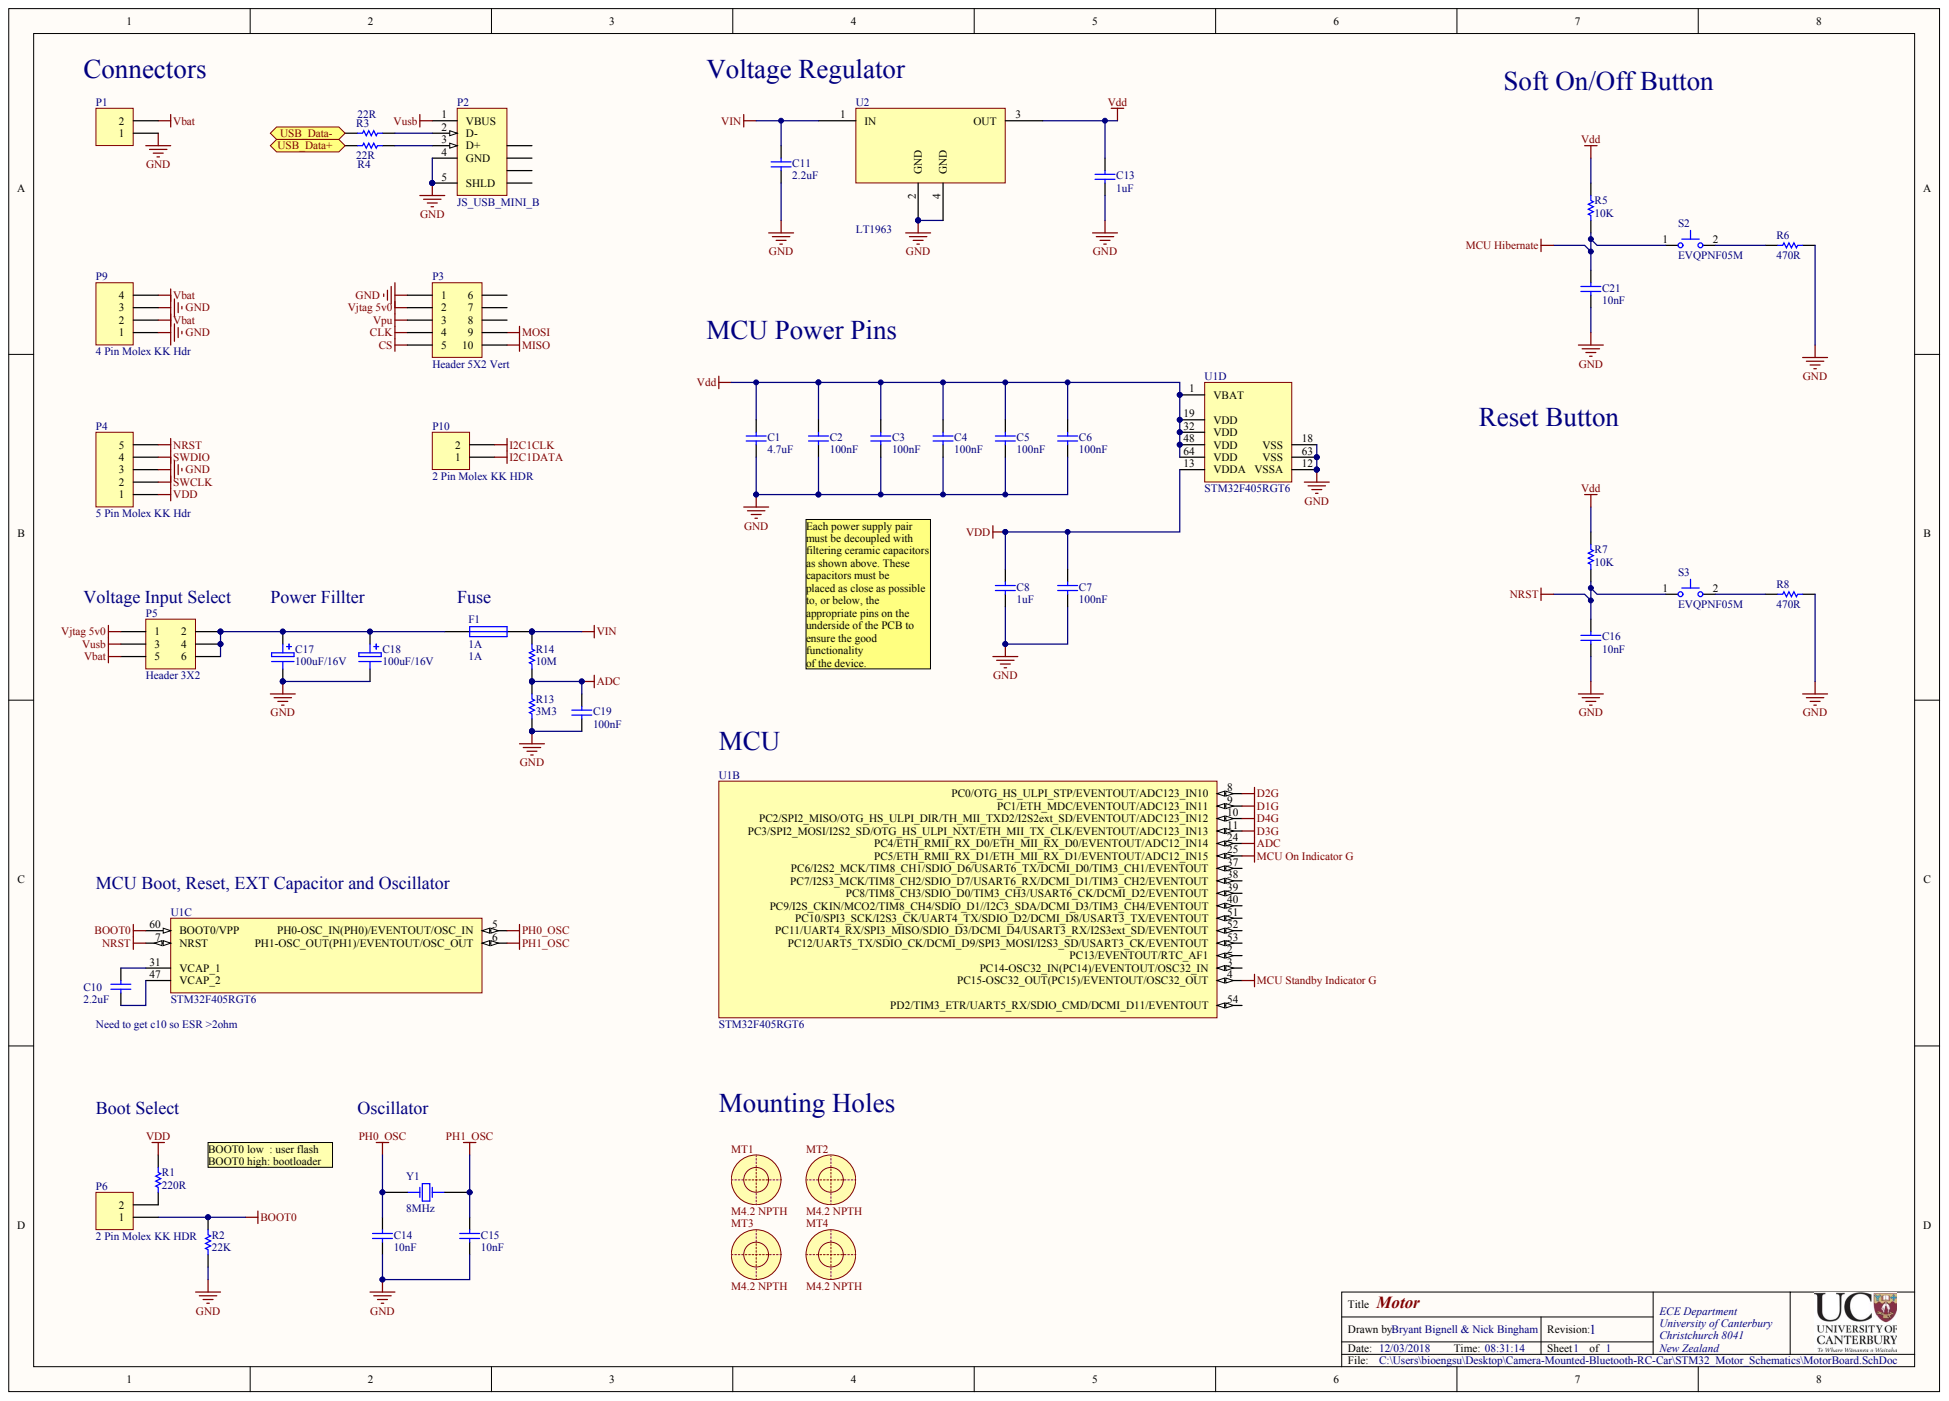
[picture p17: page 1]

Soft On/Off Button

4 Pin Molex KK Hdr 34

5 Pin Molex KK Hdr 345

2 Pin Molex KK HDR 12

filtering ceramic capacitors
as shown above. These
capacitors must be
placed as close as possible
to, or below, the
appropriate pins on the
underside of the PCB to
ensure the good
functionality
of the device.

MCU Boot, Reset, EXT Capacitor and Oscillator

Need to get c10 so ESR >2ohm

Motor Title | ECE Department University of Canterbury Christchurch 8041 New Zealand

Drawn by: Bryant Bignell & Nick Bingham | Revision: 1

Date: 12/03/2018 Time: 08:31:14 | Sheet 1 of 1

C:\Users\bioengsu\Desktop\Camera-Mounted-Bluetooth-RC-Car\STM32_Motor_Schematics\MotorBoard.SchDoc

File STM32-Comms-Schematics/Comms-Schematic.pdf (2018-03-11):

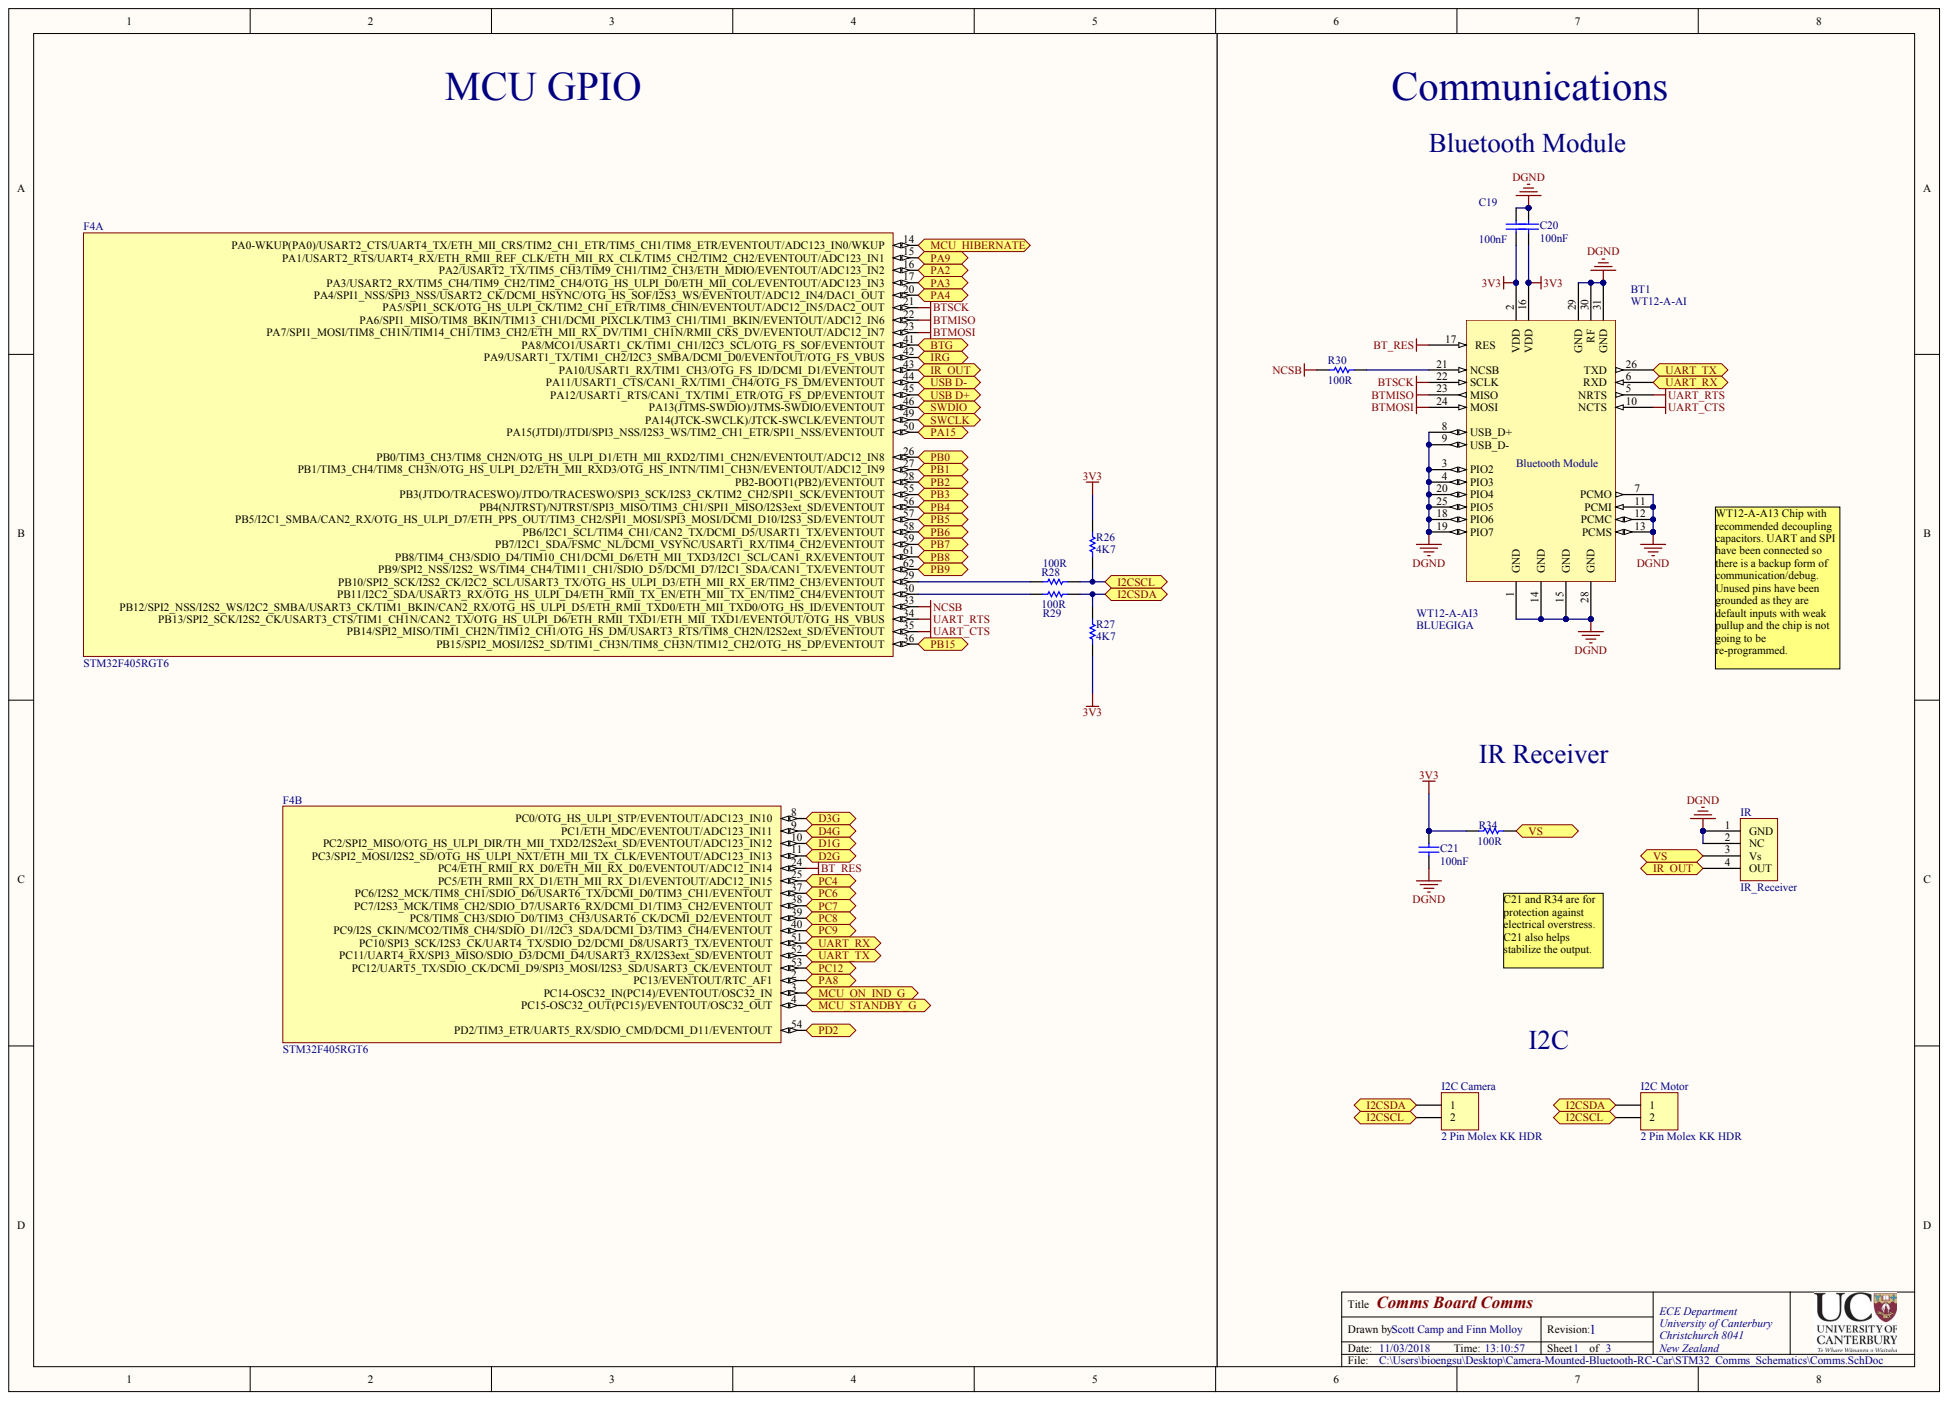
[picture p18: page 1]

WT12-A-A13 Chip with
mended decoupling
recom
capacitors. UART and SPI
have been connected so
there is a backup form of
munication/debug.
com
Unused pins have been
grounded as they are
default inputs with weak
pullup and the chip is not
going to be
re-program

2 Pin Molex KK HDR 12

Comms Board Comms Title | ECE Department University of Canterbury Christchurch 8041 New Zealand

Drawn by: Scott Camp and Finn Molloy | Revision: 1

Date: 11/03/2018 Time: 13:10:57 | Sheet 1 of 3

C:\Users\bioengsu\Desktop\Camera-Mounted-Bluetooth-RC-Car\STM32_Com

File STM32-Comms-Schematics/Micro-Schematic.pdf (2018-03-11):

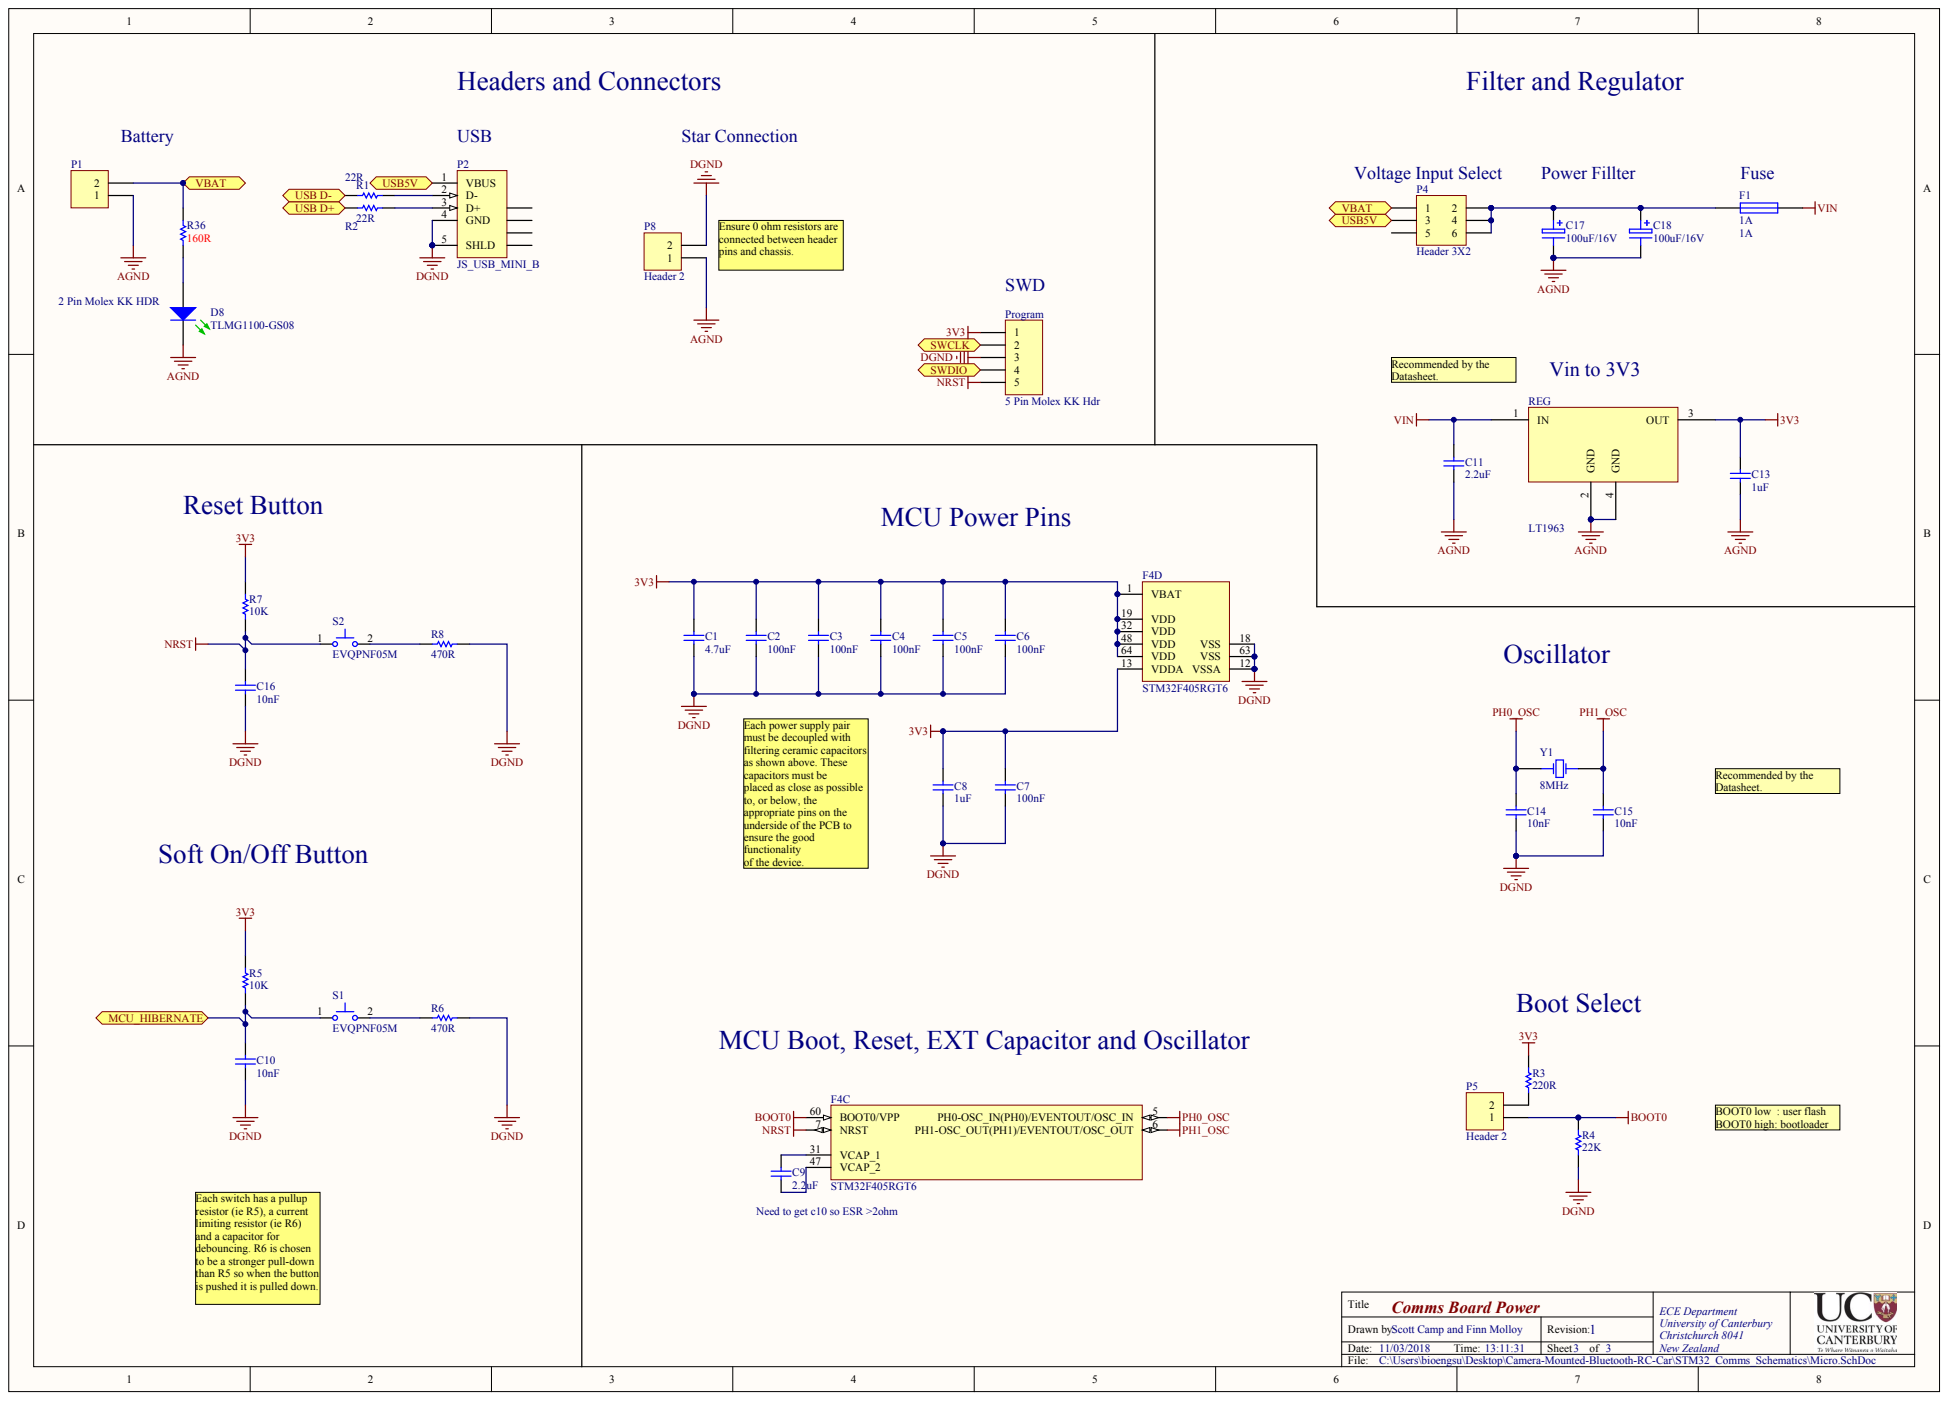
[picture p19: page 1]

Ensure 0 ohm resistors are
connected between header
pins and chassis.

2 Pin Molex KK HDR

5 Pin Molex KK Hdr

MCU Power Pins

VDDA 13

Each power supply pair
must be decoupled with
filtering ceramic capacitors
as shown above. These
capacitors must be
placed as close as possible
to, or below, the
appropriate pins on the
underside of the PCB to
ensure the good
functionality
of the device.

Soft On/Off Button

MCU Boot, Reset, EXT Capacitor and Oscillator

Each switch has a pullup
resistor (ie R5), a current
limiting resistor (ie R6)
and a capacitor for
debouncing. R6 is chosen
to be a stronger pull-down
than R5 so when the button
is pushed it is pulled down.

Need to get c10 so ESR >2ohm

Title Comms Board Power | ECE Department University of Canterbury Christchurch 8041 New Zealand

Drawn by: Scott Camp and Finn Molloy | Revision: 1

Date: 11/03/2018 Time: 13:11:31 | Sheet 3 of 3

C:\Users\bioengsu\Desktop\Camera-Mounted-Bluetooth-RC-Car\STM32_Comms_Schematics\Micro.SchDoc

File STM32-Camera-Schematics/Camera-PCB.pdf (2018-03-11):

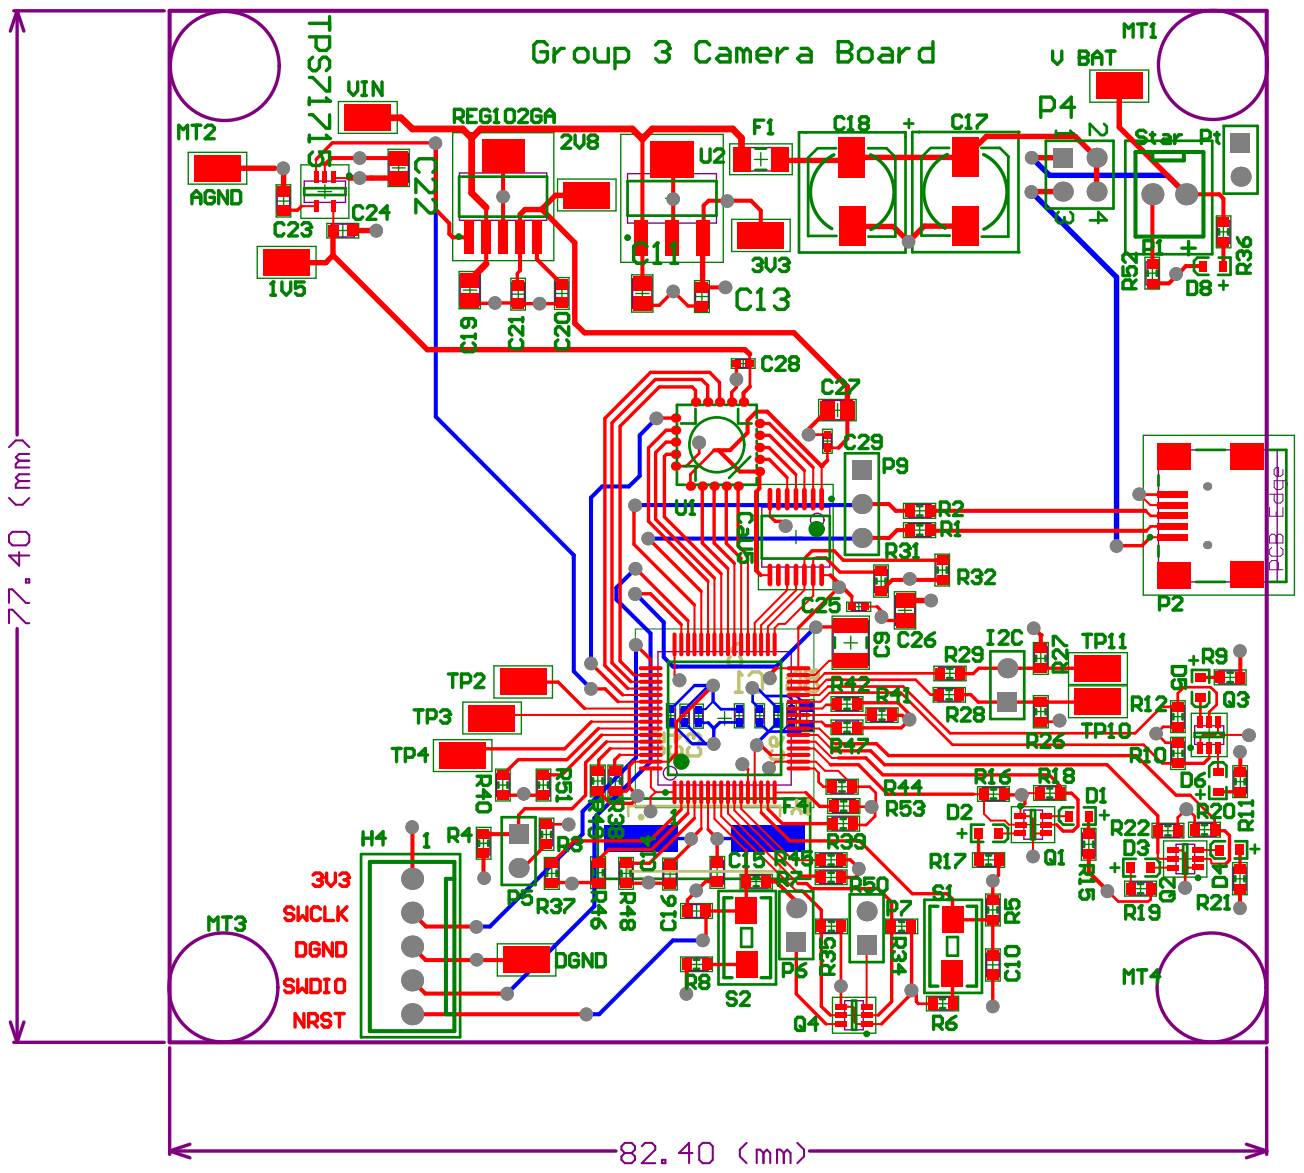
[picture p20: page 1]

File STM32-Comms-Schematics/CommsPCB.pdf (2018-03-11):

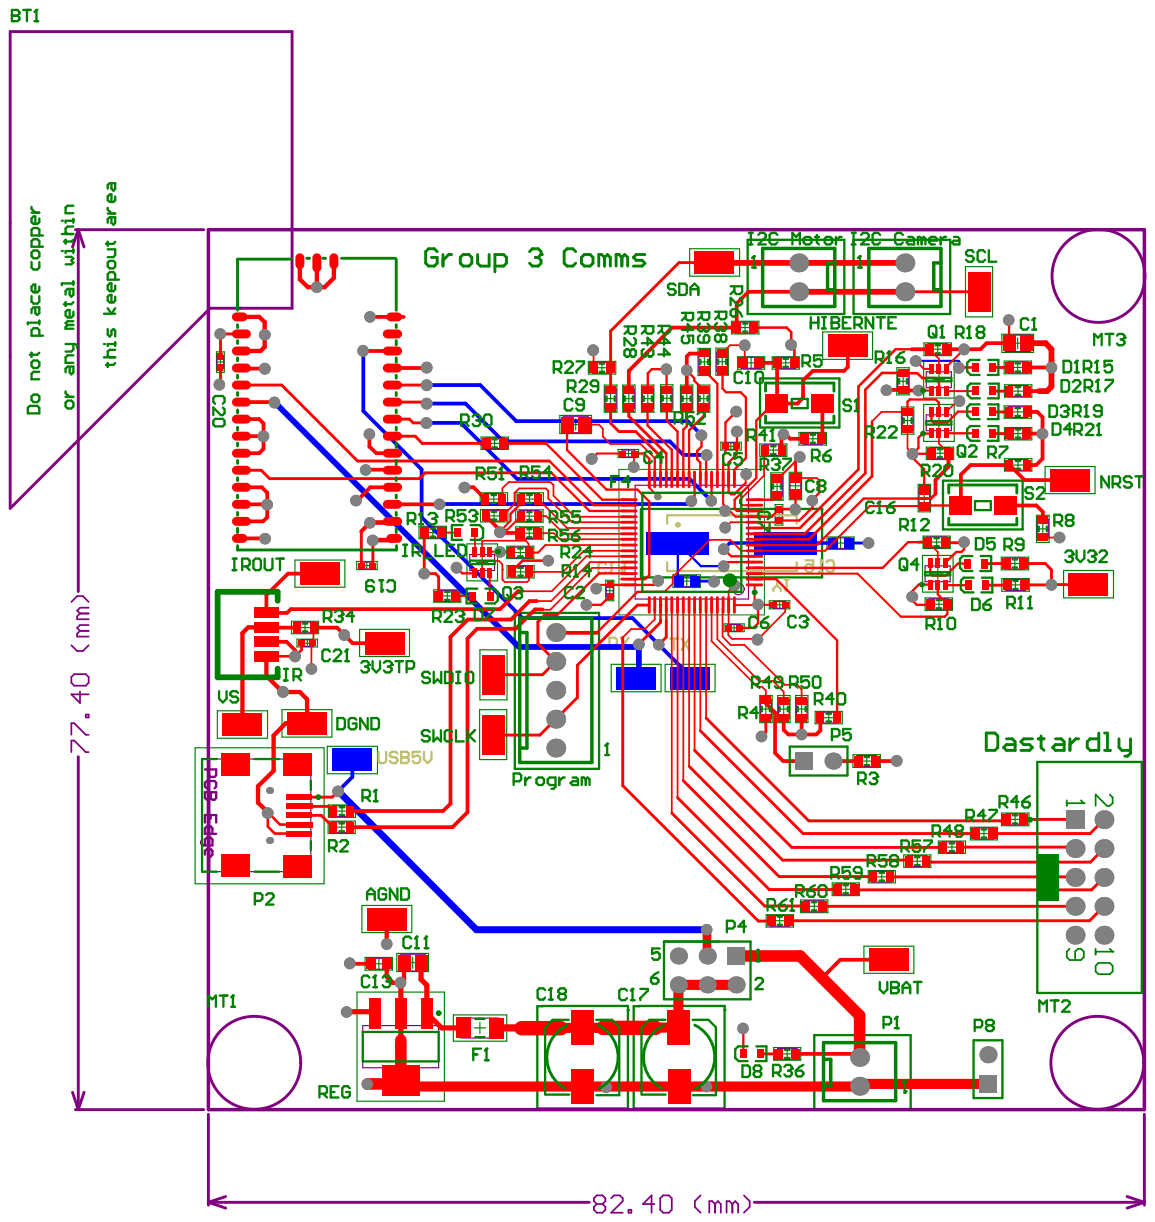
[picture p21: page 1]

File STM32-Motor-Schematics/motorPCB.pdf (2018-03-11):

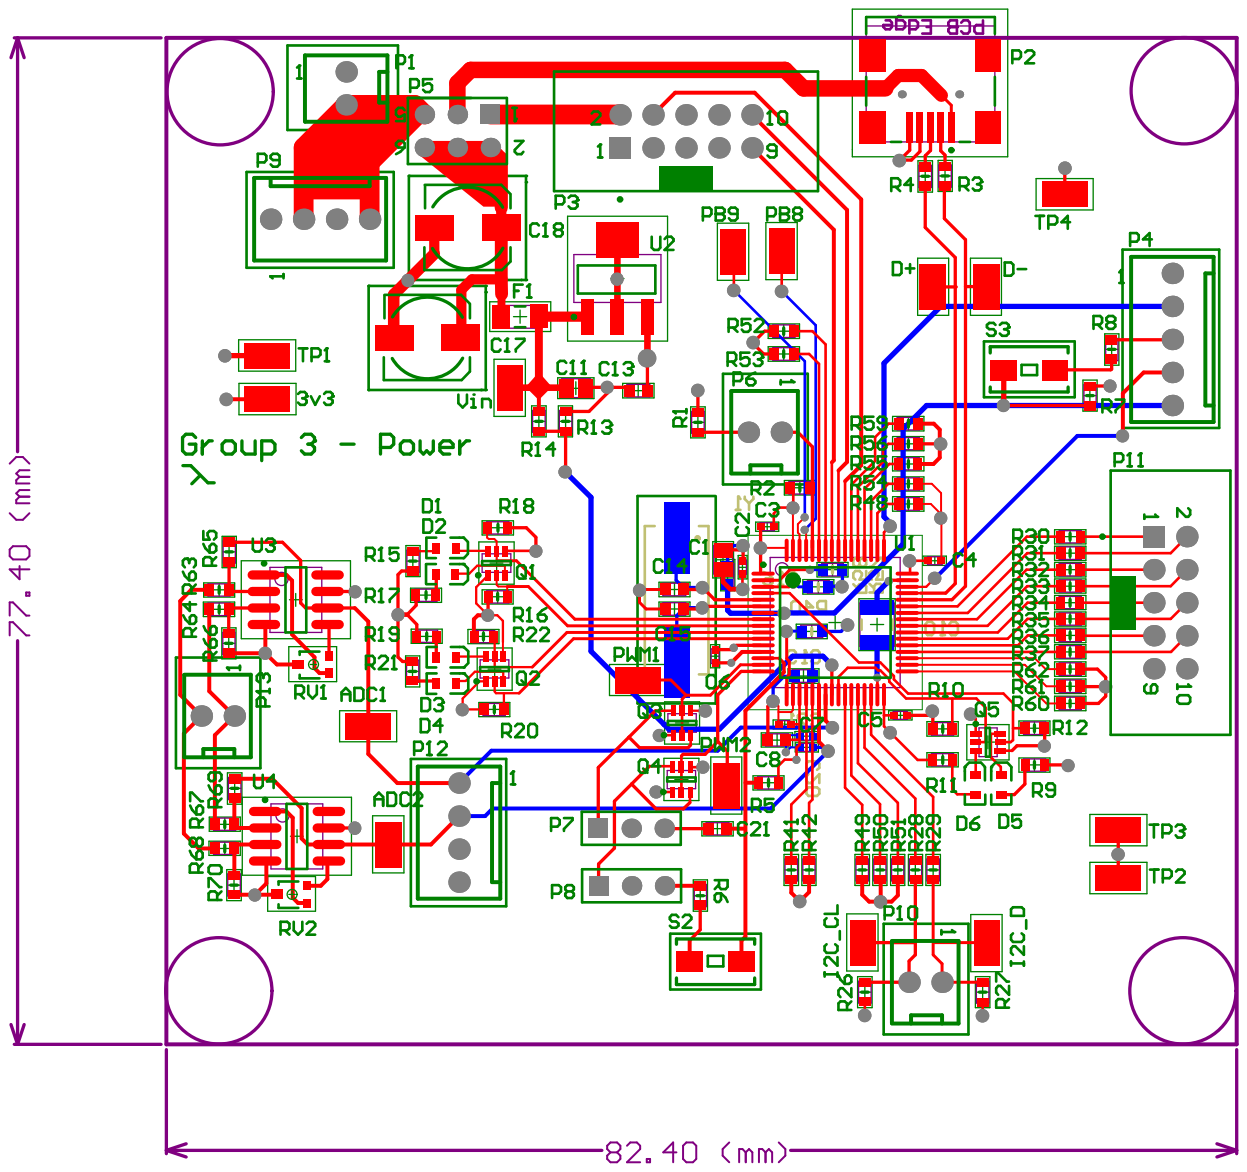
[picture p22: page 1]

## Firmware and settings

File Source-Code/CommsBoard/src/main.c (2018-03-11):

/**
*****************************************************************************
**
**  File        : main.c
**
**  Abstract    : main function.
**
**  Functions   : main
**
**  Environment : Atollic TrueSTUDIO(R)
**                STMicroelectronics STM32F4xx Standard Peripherals Library
**
*****************************************************************************
*/

/* Includes */
#include "main.h"
#include "stm32f4xx.h"
#include "ir.h"

#include "uart.h"
#include "led.h"
#include "button.h"
#include "timer.h"
#include "standby.h"
#include "i2c.h"
#include "debug_gpio.h"

#define BATMAN 1

//static uint8_t lastButtonStatus = RESET;
static u16 currentLed = 0;
static u32 currentTime = 0;

int wheel_angle = 0;
int motor_speed = 0;
long unsigned int sysTick;

void init_all()
{


	led_init();
	button_init();
	timer_init();
	standby_init();
	uart_init();
	debug_gpio_init();
	i2c_init();

	led_on(STATUS_LED_ON);
}

int main() {
    init();
    uint16_t ir_data = 0;

    int i=0;
    init_all();
    while(1){


    	for(i=-100;i<100;i++){
    		i2c_set_speed(i);
    	}

    	for(i=100;i>-100;i--){
    		i2c_set_speed(i);
    	}

    	//uart_send("World\n\r");






    }



    ir_rc5_rx_init();
    //initExtInterrupt();
	//initClkInterrupt();
    while(BATMAN)
    {
    	ir_data = ir_rc5_rx_read();
    	MOTORCONTROL(ir_data);


        //loop();
	}
}

void init() {
    RCC_AHB1PeriphClockCmd(RCC_AHB1Periph_GPIOC, ENABLE);
    GPIO_InitTypeDef gpio;
    GPIO_StructInit(&gpio);
    gpio.GPIO_Mode = GPIO_Mode_OUT;
    gpio.GPIO_Pin = LEDS;
    GPIO_Init(GPIOC, &gpio);


}

void initButton() {
    RCC_AHB1PeriphClockCmd(RCC_AHB1Periph_GPIOA, ENABLE);

    GPIO_InitTypeDef gpio;
    GPIO_StructInit(&gpio);
    gpio.GPIO_Mode = GPIO_Mode_IN;
    gpio.GPIO_Pin = GPIO_Pin_0;
    GPIO_Init(GPIOA, &gpio);
}

void initButtonLED() {
	RCC_AHB1PeriphClockCmd(RCC_AHB1Periph_GPIOC, ENABLE);
	GPIO_InitTypeDef gpio;
	GPIO_StructInit(&gpio);
	gpio.GPIO_Mode = GPIO_Mode_OUT;
	gpio.GPIO_Pin = GPIO_Pin_14;
	GPIO_Init(GPIOC, &gpio);
}

void loop() {
	__NOP();
    //static uint32_t counter = 0;

    //uint8_t currentButtonStatus = GPIO_ReadInputDataBit(GPIOA, GPIO_Pin_0);

	//if (lastButtonStatus != currentButtonStatus && currentButtonStatus != RESET) {
	//	GPIO_ToggleBits(GPIOC, GPIO_Pin_14);
	//}
    //lastButtonStatus = currentButtonStatus;

    //++counter;

    //GPIO_ResetBits(GPIOC, LEDS);
    //GPIO_SetBits(GPIOC, LED[counter % 4]);

    //delay(50);
	uint16_t data = 0;
	data = ir_rc5_rx_read();

	if (data == 12320) {
		GPIO_ToggleBits(GPIOC, GPIO_Pin_0);
	}
	if (data == 12304) {
		GPIO_ToggleBits(GPIOC, GPIO_Pin_3);
	}
	if (data == 12321) {
		GPIO_ToggleBits(GPIOC, GPIO_Pin_1);
	}
	if (data == 12305) {
		GPIO_ToggleBits(GPIOC, GPIO_Pin_2);
	}
}

void delay(uint32_t ms) {
    ms *= 3360;
    while(ms--) {
        __NOP();
    }
}

void toggleLed(void) {
    if (currentTime % 200 == 0) {
        GPIO_ToggleBits(GPIOC, LED[currentLed]);
    }
}



void initExtInterrupt() {
    EXTI_InitTypeDef   EXTI_InitStructure;

    RCC_APB2PeriphClockCmd(RCC_APB2Periph_SYSCFG, ENABLE);
    SYSCFG_EXTILineConfig(EXTI_PortSourceGPIOA,EXTI_PinSource0);
    EXTI_InitStructure.EXTI_Line = EXTI_Line0;
    EXTI_InitStructure.EXTI_Mode = EXTI_Mode_Interrupt;
    EXTI_InitStructure.EXTI_Trigger = EXTI_Trigger_Rising;
    EXTI_InitStructure.EXTI_LineCmd = ENABLE;
    EXTI_Init(&EXTI_InitStructure);

    NVIC_InitTypeDef NVIC_InitStructure;

    NVIC_InitStructure.NVIC_IRQChannel = EXTI0_IRQn;
    NVIC_InitStructure.NVIC_IRQChannelPreemptionPriority = 0x0F;
    NVIC_InitStructure.NVIC_IRQChannelSubPriority = 0x0F;
    NVIC_InitStructure.NVIC_IRQChannelCmd = ENABLE;
    NVIC_Init(&NVIC_InitStructure);
}


void switchLed(void) {
    GPIO_ResetBits(GPIOC, LED[currentLed]);

    currentLed++;
    if (currentLed > 3) {
        currentLed = 0;
    }
}


void MOTORCONTROL(data)
{
	if (data == 12320)
    {
       	if(motor_speed>=0)
       	{
       	   	motor_speed += 2;
       	}
       	else
       	{
       		motor_speed = 0;
       	}
    }
    else if (data == 12304)
    {
      	wheel_angle -= 2;
    }
    else if (data == 12321)
    {
      	if(motor_speed<=0)
       	{
       		motor_speed -= 2;
       	}
      	else
      	{
      		motor_speed = 0;
      	}
    }
    else if (data == 12305)
    {
       	wheel_angle += 2;
    }
    else
    {
       	if(motor_speed>0)
       	{
       		motor_speed -=1;
       	}
       	else if(motor_speed<0)
       	{
       		motor_speed +=1;
       	}
    }
}

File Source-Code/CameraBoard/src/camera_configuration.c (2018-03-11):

/*
 * camera_configuration.c
 *
 *  Created on: May 28, 2013
 *      Author: mlk28
 */

/* Includes */
#include "camera_configuration.h"
#include "stm32f4xx.h"
#include "stm32f4xx_gpio.h"
#include "stm32f4xx_tim.h"
#include "stm32f4xx_i2c.h"
#include "system_stm32f4xx.h"
#include "stm32f4xx_rcc.h"

#include "i2c_message.h"
#include "led.h"
#include "camera_pwm.h"
#include "debug_gpio.h"

//Camera Globals
int begin_camera_data=0;
uint16_t vert_index=0;
uint16_t horz_index=0;
uint16_t bits_index=0;

#define HORZ_LENGTH 256
#define VERT_LENGTH 96
#define SLOWED_EXT_CLK 10 // 200 works


#define data_bit_0 GPIO_ReadInputDataBit(GPIOC, GPIO_Pin_12)
#define data_bit_1 GPIO_ReadInputDataBit(GPIOA, GPIO_Pin_10)
#define data_bit_2 GPIO_ReadInputDataBit(GPIOA, GPIO_Pin_9)
#define data_bit_3 GPIO_ReadInputDataBit(GPIOA, GPIO_Pin_8)
#define data_bit_4 GPIO_ReadInputDataBit(GPIOC, GPIO_Pin_9)
#define data_bit_5 GPIO_ReadInputDataBit(GPIOC, GPIO_Pin_8)
#define data_bit_6 GPIO_ReadInputDataBit(GPIOC, GPIO_Pin_7)
#define data_bit_7 GPIO_ReadInputDataBit(GPIOC, GPIO_Pin_6)
#define data_bit_HD GPIO_ReadInputDataBit(GPIOC, GPIO_Pin_10)
#define data_bit_VD GPIO_ReadInputDataBit(GPIOC, GPIO_Pin_11)

extern uint8_t outBuffer[HORZ_LENGTH*VERT_LENGTH];


uint8_t image_count=0;

void camera_configuration_init(void){

	//Initiate Debug GPIO
	GPIO_InitTypeDef  GPIO_InitStructure;

	//Initiate on Port B
	RCC_AHB1PeriphClockCmd(RCC_AHB1Periph_GPIOD, ENABLE);

	GPIO_InitStructure.GPIO_Pin = GPIO_Pin_14;
	GPIO_InitStructure.GPIO_Mode = GPIO_Mode_OUT;
	GPIO_InitStructure.GPIO_OType = GPIO_OType_PP;
	GPIO_InitStructure.GPIO_Speed = GPIO_Speed_100MHz;
	GPIO_InitStructure.GPIO_PuPd = GPIO_PuPd_NOPULL;

	GPIO_Init(GPIOB,&GPIO_InitStructure);

	//Initiate on Port D
	RCC_AHB1PeriphClockCmd(RCC_AHB1Periph_GPIOD, ENABLE);

	GPIO_InitStructure.GPIO_Pin = GPIO_Pin_2;
	GPIO_InitStructure.GPIO_Mode = GPIO_Mode_OUT;
	GPIO_InitStructure.GPIO_OType = GPIO_OType_PP;
	GPIO_InitStructure.GPIO_Speed = GPIO_Speed_100MHz;
	GPIO_InitStructure.GPIO_PuPd = GPIO_PuPd_NOPULL;

	GPIO_Init(GPIOD,&GPIO_InitStructure);


    //Configure GPIO_inputs
	//A
	RCC_AHB1PeriphClockCmd(RCC_AHB1Periph_GPIOA, ENABLE);

	GPIO_InitStructure.GPIO_Pin = GPIO_Pin_8|GPIO_Pin_9|GPIO_Pin_10|GPIO_Pin_15;  //3,2,1,DCLK
	GPIO_InitStructure.GPIO_Mode = GPIO_Mode_IN;
	GPIO_InitStructure.GPIO_OType = GPIO_OType_PP;
	GPIO_InitStructure.GPIO_Speed = GPIO_Speed_100MHz;
	GPIO_InitStructure.GPIO_PuPd = GPIO_PuPd_NOPULL;
	GPIO_Init(GPIOA,&GPIO_InitStructure);

	//C
	RCC_AHB1PeriphClockCmd(RCC_AHB1Periph_GPIOC, ENABLE);
	GPIO_InitStructure.GPIO_Pin = GPIO_Pin_6|GPIO_Pin_7|GPIO_Pin_8|GPIO_Pin_9|GPIO_Pin_12|GPIO_Pin_10|GPIO_Pin_11;  //7,6,5,4,0,HD,VD
	GPIO_InitStructure.GPIO_Mode = GPIO_Mode_IN;
	GPIO_InitStructure.GPIO_OType = GPIO_OType_PP;
	GPIO_InitStructure.GPIO_Speed = GPIO_Speed_100MHz;
	GPIO_InitStructure.GPIO_PuPd = GPIO_PuPd_NOPULL;
	GPIO_Init(GPIOC,&GPIO_InitStructure);

	//Camera PWM
	camera_pwm_config(1);
	camera_pwm_set_dc((2*(10000-1500+50*5))/10000);
}



void camera_configuration_reset(void){

	//Reset Cam
	led_on(DEBUG_LED_0);
	GPIO_ResetBits(GPIOB, GPIO_Pin_14);  // Turn CAM Rest High
	timer_ms_delay(100);
	debug_gpio_on(GPIOD, GPIO_Pin_2);  // Turn on Regs
	timer_ms_delay(100);

	GPIO_SetBits(GPIOB, GPIO_Pin_14);  //Turn Reset Off
	led_off(DEBUG_LED_0);
	timer_ms_delay(100);
}

void camera_configuration_interupt_init(void){

    //DCLK INT
	//Enable clock for GPIOA 15 DCLK
    RCC_APB2PeriphClockCmd(RCC_APB2Periph_SYSCFG, ENABLE);
	RCC_AHB1PeriphClockCmd(RCC_AHB1Periph_GPIOA, ENABLE);
	InitGPIO(GPIOA, GPIO_Pin_15, GPIO_Mode_IN); //initialise PA0 is input
	 //attach interrupt to GPIO
	Attach_GPIO_Interrupt(EXTI_PortSourceGPIOA, EXTI_PinSource15, EXTI_Line15 ,EXTI_Trigger_Falling, 0 );


    //VD INT
	//Enable clock for GPIOC 11 DCLK
    RCC_APB2PeriphClockCmd(RCC_APB2Periph_SYSCFG, ENABLE);
	RCC_AHB1PeriphClockCmd(RCC_AHB1Periph_GPIOC, ENABLE);
	InitGPIO(GPIOC, GPIO_Pin_11, GPIO_Mode_IN); //initialise PA0 is input
	 //attach interrupt to GPIO
	Attach_GPIO_Interrupt(EXTI_PortSourceGPIOC, EXTI_PinSource11, EXTI_Line11 ,EXTI_Trigger_Rising, 0 );


    //HD INT
	//Enable clock for GPIOC 11 DCLK
    RCC_APB2PeriphClockCmd(RCC_APB2Periph_SYSCFG, ENABLE);
	RCC_AHB1PeriphClockCmd(RCC_AHB1Periph_GPIOC, ENABLE);
	InitGPIO(GPIOC, GPIO_Pin_10, GPIO_Mode_IN); //initialise PA0 is input
	 //attach interrupt to GPIO
	Attach_GPIO_Interrupt(EXTI_PortSourceGPIOC, EXTI_PinSource10, EXTI_Line10 ,EXTI_Trigger_Rising, 0 );

}


void camera_configuration_interupt_deinit(void){
	EXTI_DeInit();
}
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

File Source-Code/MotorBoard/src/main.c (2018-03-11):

/**
*****************************************************************************
**
**  File        : main.c
**
**  Abstract    : main function.
**
**  Functions   : main
**
**  Environment : Atollic TrueSTUDIO(R)
**                STMicroelectronics STM32F4xx Standard Peripherals Library
**
**  Distribution: The file is distributed “as is,” without any warranty
**                of any kind.
**
**  (c)Copyright Atollic AB.
**  You may use this file as-is or modify it according to the needs of your
**  project. This file may only be built (assembled or compiled and linked)
**  using the Atollic TrueSTUDIO(R) product. The use of this file together
**  with other tools than Atollic TrueSTUDIO(R) is not permitted.
**
*****************************************************************************
*/

/* Includes */
#include <stdio.h>
#include <stm32f4xx.h>
#include <stm32f4xx_rcc.h>
#include <stm32f4xx_gpio.h>
#include "led.h"
#include "timer.h"
#include "button.h"
#include "standby.h"
#include "i2c.h"
#include "uart.h"
#include "debug_gpio.h"
#include "motor_pwm.h"
#include "motor_adc.h"

//ADC variables:
long int batteryVoltage=0;
long int emfVoltage=0;
long int bemfVoltage=0;

//I2C variables:
extern short int transmissionMode;
long unsigned int sysTick=0;
extern long unsigned int i2cErrorCount;
extern long unsigned int startCount;
extern long unsigned int dataCount;
extern long unsigned int stopCount;
char inBuffer[21];
char outBuffer[21];

//Print variable
extern char outstr[200];

//Motor variable
extern int forwardMode;

//Flags
extern long int speedFlag;
extern long int speedValue;
extern long int angleFlag;
extern long int angleValue;

int main(void)
{
    int i = 0;
    //int current_adc_value = 0;

    SystemInit();
    debug_gpio_init();
    led_init();
    timer_init();
    standby_init();
    //button_init(); // Don't put this in if using standby_init
    uart_init();
    i2c_init();
    motor_pwm_init();
    motor_adc_init();

    motor_pwm_config(PERIOD_100HZ);
    led_on(STATUS_LED_ON);


    inBuffer[21] = '\0';
    for (i=0; i<20; i++){
    	inBuffer[i] = 'z';
    }

    outBuffer[21] = '\0';
    for (i=0; i<10; i++){
    	outBuffer[i] = 'A'+(char)i;
    }
    outBuffer[i] = '\0';

    sprintf(outstr, "                                                                              ");
    uart_send(outstr);
    //debug_gpio_on(DEBUG_GPIO_4);

    /*motor_pwm_config(10000); //50Hz
    motor_pwm_set_dc(2,5000);
    motor_pwm_set_dc(3,5000);*/

    print_battery_voltage();

    while (1)
    {
    	//debug_gpio_toggle(DEBUG_GPIO_3);
    	/*set_bat_str();
    	i2c_transfer_report();
    	uart_send("\n");

    	set_speed_read_str();
    	i2c_transfer_report();
    	uart_send("\n");

    	set_speed_write_str();
    	i2c_transfer_report();
    	uart_send("\n");

    	set_angle_read_str();
    	i2c_transfer_report();
    	uart_send("\n");

    	set_angle_write_str();
    	i2c_transfer_report();
    	uart_send("\n");*/



    	/*motor_set_angle(3, 100);
    	timer_ms_delay(50);
    	motor_set_angle(3, 0);
    	timer_ms_delay(50);
    	motor_set_angle(3, -100);
    	timer_ms_delay(50);*/
    	if (speedFlag){
    		sprintf(outstr, "\n%i\n", speedValue);
    		uart_send(outstr);
    		if (speedValue>=0) {
    			motor_forward_speed(speedValue);
    		}
    		if (speedValue<0) {
    			motor_back_speed(-speedValue);
    		}
    		speedFlag=0;
    	}
    	if (angleFlag){
    		GPIO_PinAFConfig(GPIOA, GPIO_PinSource2, GPIO_AF_TIM9);
    		sprintf(outstr, "\n%i\n", angleValue);
    		uart_send(outstr);
    		motor_set_angle(3, angleValue);
    		angleFlag=0;
    		//timer_ms_delay(200);
    		//GPIO_PinAFConfig(GPIOA, GPIO_PinSource2, GPIO_AF_TIM12);
    	}
    	//sprintf(outstr, "\nANGLE: %i\n", angleValue);
    	//uart_send(outstr);
    	//motor_set_angle(3, angleValue);

    	i2c_transfer_report();
    	//uart_send("     \n");
    	/*uart_send("\n");
    	print_battery_voltage();
    	uart_send("\n");
    	print_emf_voltage();
    	uart_send("\n");*/
    	//print_bemf_voltage();
    }
}

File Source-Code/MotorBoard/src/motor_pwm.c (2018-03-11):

/*
 * motor_pwm.c
 *
 *  Created on: May 22, 2013
 *      Author: nbb23
 */

#include "motor_pwm.h"
#include "uart.h"
#include <stdio.h>

int forwardMode = 1;
extern char outstr[200];
// TODO: Needs to be updated to use two different TIMs

void motor_pwm_init() {

}

void motor_pwm_config(int period)
{
	TIM_TimeBaseInitTypeDef TIM_TimeBaseStructure;
	TIM_OCInitTypeDef TIM_OCInitStructure;
	GPIO_InitTypeDef GPIO_InitStructure;

	uint16_t PrescalerValue = 0;
	/* Compute the prescaler value */
	PrescalerValue = (uint16_t) ((SystemCoreClock /2) / 2800000) - 1;


	/* TIM5 clock enable */
	RCC_APB1PeriphClockCmd(RCC_APB1Periph_TIM5, ENABLE);

	/* GPIOA clock enable */
	RCC_AHB1PeriphClockCmd(RCC_AHB1Periph_GPIOA, ENABLE);

	/* GPIOA Configuration: TIM5 CH2 (PA1) and TIM2 CH3 (PA2) */
	GPIO_InitStructure.GPIO_Pin = GPIO_Pin_1 ;
	GPIO_InitStructure.GPIO_Mode = GPIO_Mode_AF;
	GPIO_InitStructure.GPIO_Speed = GPIO_Speed_100MHz;
	GPIO_InitStructure.GPIO_OType = GPIO_OType_PP;
	GPIO_InitStructure.GPIO_PuPd = GPIO_PuPd_UP ;
	GPIO_Init(GPIOA, &GPIO_InitStructure);

	/* Connect TIM5 pins to AF2 and TIM2 pins to AF1 */
	GPIO_PinAFConfig(GPIOA, GPIO_PinSource1, GPIO_AF_TIM5);

	/* Time base configuration - TIM5 */
	TIM_TimeBaseStructure.TIM_Period = period;
	TIM_TimeBaseStructure.TIM_Prescaler = PrescalerValue;
	TIM_TimeBaseStructure.TIM_ClockDivision = 0;
	TIM_TimeBaseStructure.TIM_CounterMode = TIM_CounterMode_Up;
	TIM_TimeBaseInit(TIM5, &TIM_TimeBaseStructure);
	/* PWM1 Mode configuration: Channel2 - TIM5 */
	TIM_OCInitStructure.TIM_OCMode = TIM_OCMode_PWM1;
	TIM_OCInitStructure.TIM_OutputState = TIM_OutputState_Enable;
	TIM_OCInitStructure.TIM_Pulse = 0;
	TIM_OCInitStructure.TIM_OCPolarity = TIM_OCPolarity_High;
	TIM_OC2Init(TIM5, &TIM_OCInitStructure);
	TIM_OC2PreloadConfig(TIM5, TIM_OCPreload_Enable);
	TIM_ARRPreloadConfig(TIM5, ENABLE);
	/* TIM5 enable counter */
	TIM_Cmd(TIM5, ENABLE);


	/* TIM2 clock enable */
	RCC_APB2PeriphClockCmd(RCC_APB2Periph_TIM9, ENABLE);

	/* GPIOA clock enable */
	RCC_AHB1PeriphClockCmd(RCC_AHB1Periph_GPIOA, ENABLE);

	/* GPIOA Configuration: TIM5 CH2 (PA1) and TIM2 CH3 (PA2) */
	GPIO_InitStructure.GPIO_Pin = GPIO_Pin_2 ;
	GPIO_InitStructure.GPIO_Mode = GPIO_Mode_AF;
	GPIO_InitStructure.GPIO_Speed = GPIO_Speed_100MHz;
	GPIO_InitStructure.GPIO_OType = GPIO_OType_PP;
	GPIO_InitStructure.GPIO_PuPd = GPIO_PuPd_UP ;
	GPIO_Init(GPIOA, &GPIO_InitStructure);

	/* Connect TIM5 pins to AF2 and TIM2 pins to AF1 */
	GPIO_PinAFConfig(GPIOA, GPIO_PinSource2, GPIO_AF_TIM9);

	/* Time base configuration - TIM2 */
	TIM_TimeBaseStructure.TIM_Period = period;
	TIM_TimeBaseStructure.TIM_Prescaler = PrescalerValue;
	TIM_TimeBaseStructure.TIM_ClockDivision = 0;
	TIM_TimeBaseStructure.TIM_CounterMode = TIM_CounterMode_Up;
	TIM_TimeBaseInit(TIM9, &TIM_TimeBaseStructure);
	/* PWM1 Mode configuration: Channel3 - TIM2*/
	TIM_OCInitStructure.TIM_OCMode = TIM_OCMode_PWM1;
	TIM_OCInitStructure.TIM_OutputState = TIM_OutputState_Enable;
	TIM_OCInitStructure.TIM_Pulse = 0;
	TIM_OCInitStructure.TIM_OCPolarity = TIM_OCPolarity_High;
	TIM_OC1Init(TIM9, &TIM_OCInitStructure);
	TIM_OC1PreloadConfig(TIM9, TIM_OCPreload_Enable);
	TIM_ARRPreloadConfig(TIM9, ENABLE);
	/* TIM2 enable counter */
	TIM_Cmd(TIM9, ENABLE);
}

void motor_pwm_set_dc(uint16_t channel,uint16_t dutycycle)
{
	switch (channel) {
		case 2:
			TIM5->CCR2 = dutycycle;
		case 3:
			TIM9->CCR1 = dutycycle;
	}
}

void motor_set_angle(int channel, int angle){ //-50% is 1.25, 100% is 2
	int upTime=1500+angle*5; //us, micro seconds
	motor_pwm_set_dc(channel,(PERIOD_100HZ*(10000-upTime))/10000);
}

void motor_set_speed(int channel, int power) {
	int upTime=1500+power*5; //us, micro seconds
	motor_pwm_set_dc(channel,(PERIOD_100HZ*(10000-upTime))/10000);
}

void motor_back_speed(int power) {
	if (forwardMode) {
		motor_set_speed(2, 50);
		timer_ms_delay(30);
		motor_set_speed(2, 0);
		timer_ms_delay(20);
	}
	motor_set_speed(2, power/10);
	sprintf(outstr, "Back: %i%% Power         \n", power);
	uart_send(outstr);
	forwardMode=0;
}

void motor_forward_speed(int power) {
	motor_set_speed(2, -power);
	sprintf(outstr, "Forward: %i%% Power         \n", power);
	uart_send(outstr);
	forwardMode=1;
}

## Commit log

2018-03-11 Update BoMs
    [Camera_BOM.xlsx, Comms_BOM.xlsx, Motor_BOM.xlsx]
2018-08-11 House keeping
    [Camera_Analogue.SchDoc, Camera_BoM.xlsx, Camera_Board.PrjPcb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]
